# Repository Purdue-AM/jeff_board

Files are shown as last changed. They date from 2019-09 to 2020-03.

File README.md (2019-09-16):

# jeff_board
A straightforward Arduino Nano breakout board that allows for driving 2 PWM lines up to 30V, powered on 12/24V, and connects to two thermal sensors. 
-
The jeff board was designed to clean up two temperature sensors and a fan and heater driver into one breakout board, minimizing space occupied on the VAP print-head. Below is a list of the hardware on it, with a brief justification. This device is designed for academic research VAP machines, and is implemented on the systems at Herrick Labs at Purdue University.

<b>Components</b>

<b> Arduino Nano:</b> the Nano is a small-footprint implementation of the arduino uno with some changes to make it ideal for embedded project prototyping. More information can be found on the Arduino website (https://www.arduino.cc/en/Guide/ArduinoNano). The new Arduino Nano Every is a drop-in replacement, and is a bit cheaper. Note: there are hundreds of knock-off Arduino Nanos available for a quarter of the price, most of which will work with this board. If you're not comfortable debugging electronics issues, I recommend sticking to the original.

<b>MLX90614 IR Temperature Sensor:</b> Melexis makes great IR sensors that are easy to interface with over I2C. I used Adafruit's library for this (https://learn.adafruit.com/using-melexis-mlx90614-non-contact-sensors/wiring-and-test). This is where the ambient temperature is determined as well. In the future, moving to a tighter view-angle would be good (right now it's 90deg, sub-15deg would be great). 

<b>MAX31865 RTD Amplifier and Platinum RTD Sensor:</b> I chose an RTD sensor because the reservoir sensing needs to be really accurate right around room temp. We probably won't be heating the reservoir above around 40degC, so this is a good choice. I'm using a MAX31865 breakout board from Adafruit, but there's no reason that can't be added to the PCB in the future. In fact, I'd prefer it. 

<b>MIC4427 and various power MOSFETs:</b> the MIC4427 is a low-side MOSFET driver. This is necessary to avoid over-heating, since the Arduino Nano can't provide enough current to drive the gate capacitance quickly. This should also allow some robustness for knock-off arduinos. The specific power MOSFET isn't as important, as long as it's an N-Channel rated to at least 30Vds, has a low Rdon at Vgs of 5V or lower (this will often be called a logic-level power FET), and has the same pinout in a TO-220 package. For driving the fan, you're going to want a power MOSFET with a body diode. On the jeff board in HERL, I've used IRLB3034PbF which is an extremely robust power MOSFET.

<b>DC-DC Step-Down converter:</b> This board is designed to run off of the 3D printer power supply, both 12V and 24V models. You can use any linear or switching DCDC step-down converter that fits in the TO-220 footprint with the same pinout, but my preference is the Traco Power TSR series (https://www.tracopower.com/products/browse-by-category/show/dc-dc-converters/non-isolated-step-down-regulators/tsr-1/1/). These are really reliable and temperature tolerant, and the last thing we want is the temperature control board to lose power mid-print.

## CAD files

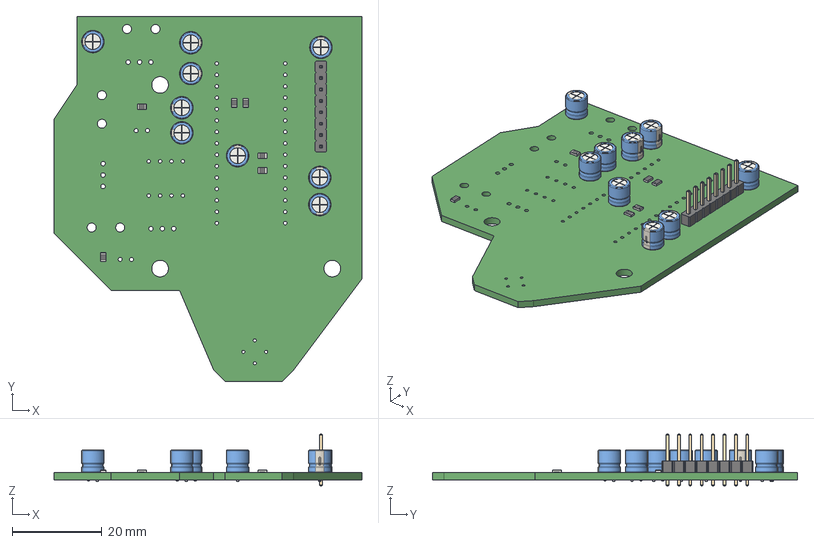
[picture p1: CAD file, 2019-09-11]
jeff_board_kicad/VAP_thermal_control.step
68.6 x 81.3 x 11.5 mm
LED_D5.0mm x 2
DIP-8_W7.62mm

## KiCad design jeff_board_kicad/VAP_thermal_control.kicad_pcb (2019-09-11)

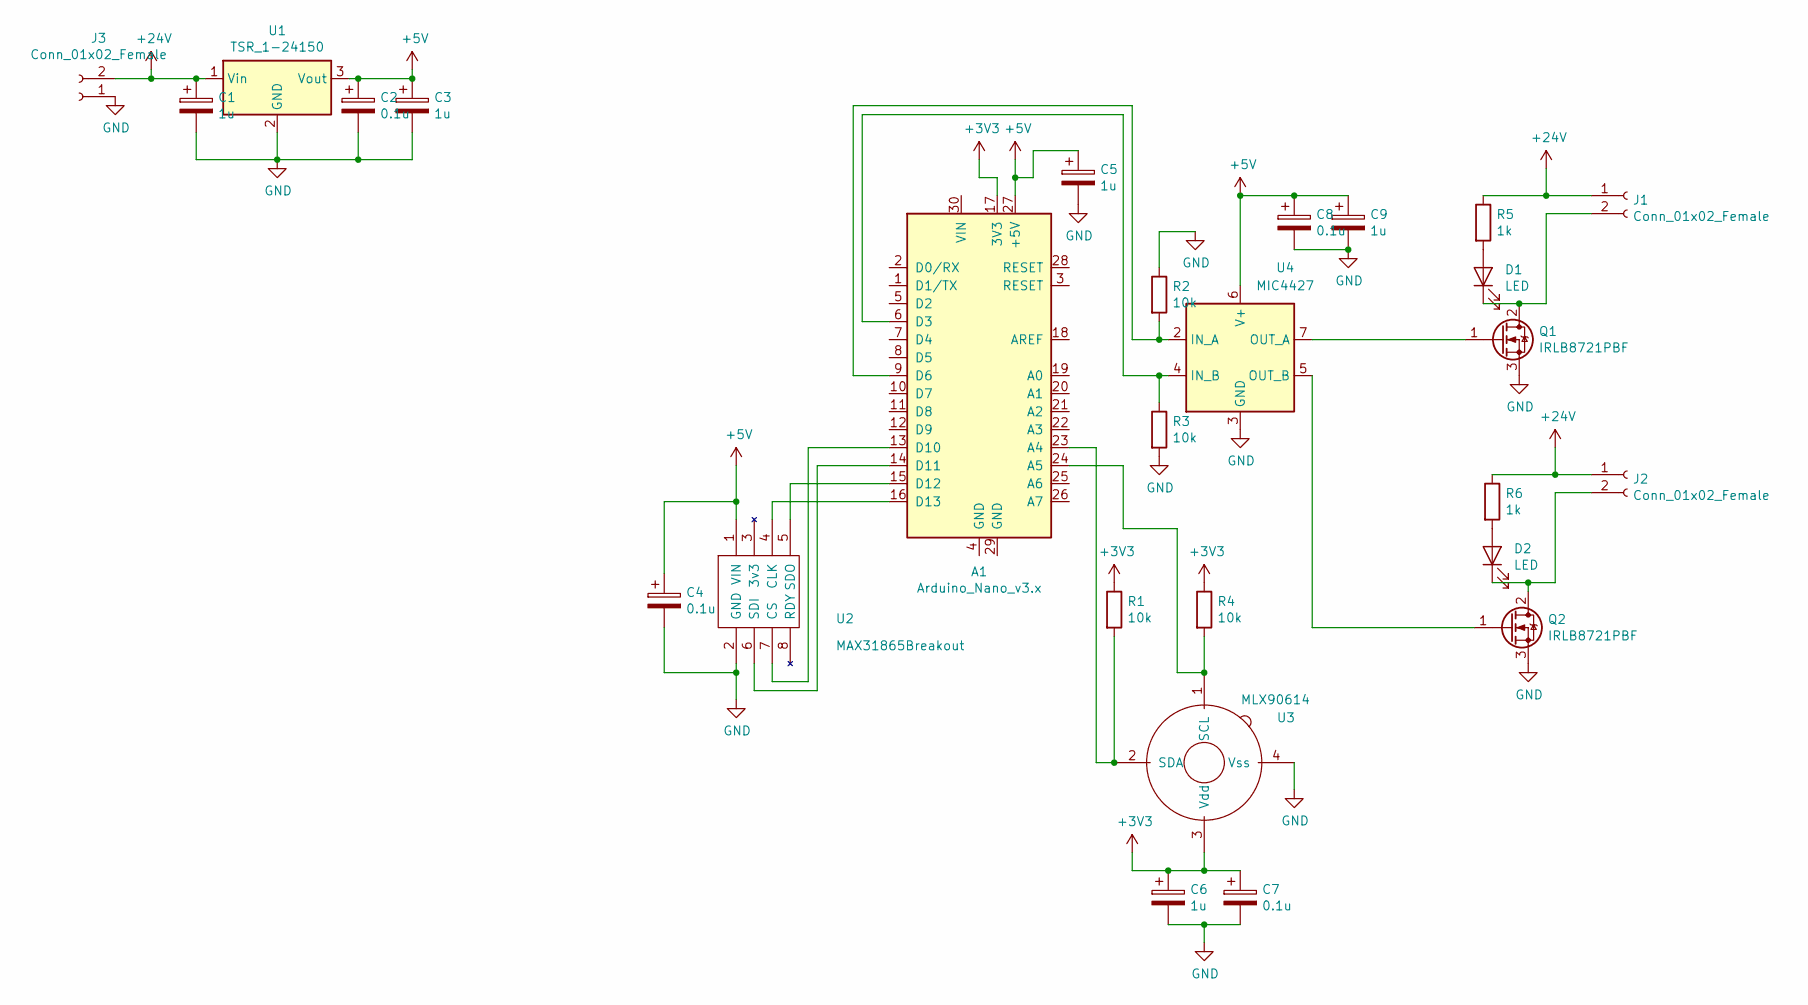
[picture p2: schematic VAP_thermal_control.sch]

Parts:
A1: Arduino_Nano_v3.x; Arduino_Nano
C1, C3, C5, C6, C9: 1u; CP_Radial_D5.0mm_P2.00mm
C2, C4, C7, C8: 0.1u; CP_Radial_D5.0mm_P2.00mm
D1, D2: LED; LED_D5.0mm
J1, J2, J3: Conn_01x02_Female; SolderWirePad_2x_2mmDrill
Q1, Q2: IRLB8721PBF; TO-220-3_Vertical
R1, R2, R3, R4: 10k; R_0805_HandSoldering
R5, R6: 1k; R_0805_HandSoldering
U1: TSR_1-24150; TO-220-3_Vertical
U2: MAX31865Breakout; Pin_Header_Straight_1x08_Pitch2.54mm
U3: MLX90614; TO-39-4_Window
U4: MIC4427; DIP-8_W7.62mm

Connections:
+3V3: A1.17 (3V3), C6.1, C7.1, R1.1, R4.1, U3.3 (Vdd)
+5V: A1.27 (+5V), C2.1, C3.1, C4.1, C5.1, C8.1, C9.1, U1.3 (Vout), U2.1 (VIN), U4.6 (V+)
+24V: C1.1, J1.1, J2.1, J3.2, R5.1, R6.1, U1.1 (Vin)
GND: A1.4 (GND), A1.29 (GND), C1.2, C2.2, C3.2, C4.2, C5.2, C6.2, C7.2, C8.2, C9.2, J3.1, Q1.3 (S), Q2.3 (S), R2.1, R3.2, U1.2 (GND), U2.2 (GND), U3.4 (Vss), U4.3 (GND)
unnamed: A1.6 (D3), R3.1, U4.4 (IN_B)
unnamed: A1.9 (D6), R2.2, U4.2 (IN_A)
unnamed: A1.13 (D10), U2.7 (CS)
unnamed: A1.14 (D11), U2.6 (SDI)
unnamed: A1.15 (D12), U2.5 (SDO)
unnamed: A1.16 (D13), U2.4 (CLK)
unnamed: A1.23 (A4), R1.2, U3.2 (SDA)
unnamed: A1.24 (A5), R4.2, U3.1 (SCL)
unnamed: D1.1 (K), J1.2, Q1.2 (D)
unnamed: D1.2 (A), R5.2
unnamed: D2.1 (K), J2.2, Q2.2 (D)
unnamed: D2.2 (A), R6.2
unnamed: Q1.1 (G), U4.7 (OUT_A)
unnamed: Q2.1 (G), U4.5 (OUT_B)

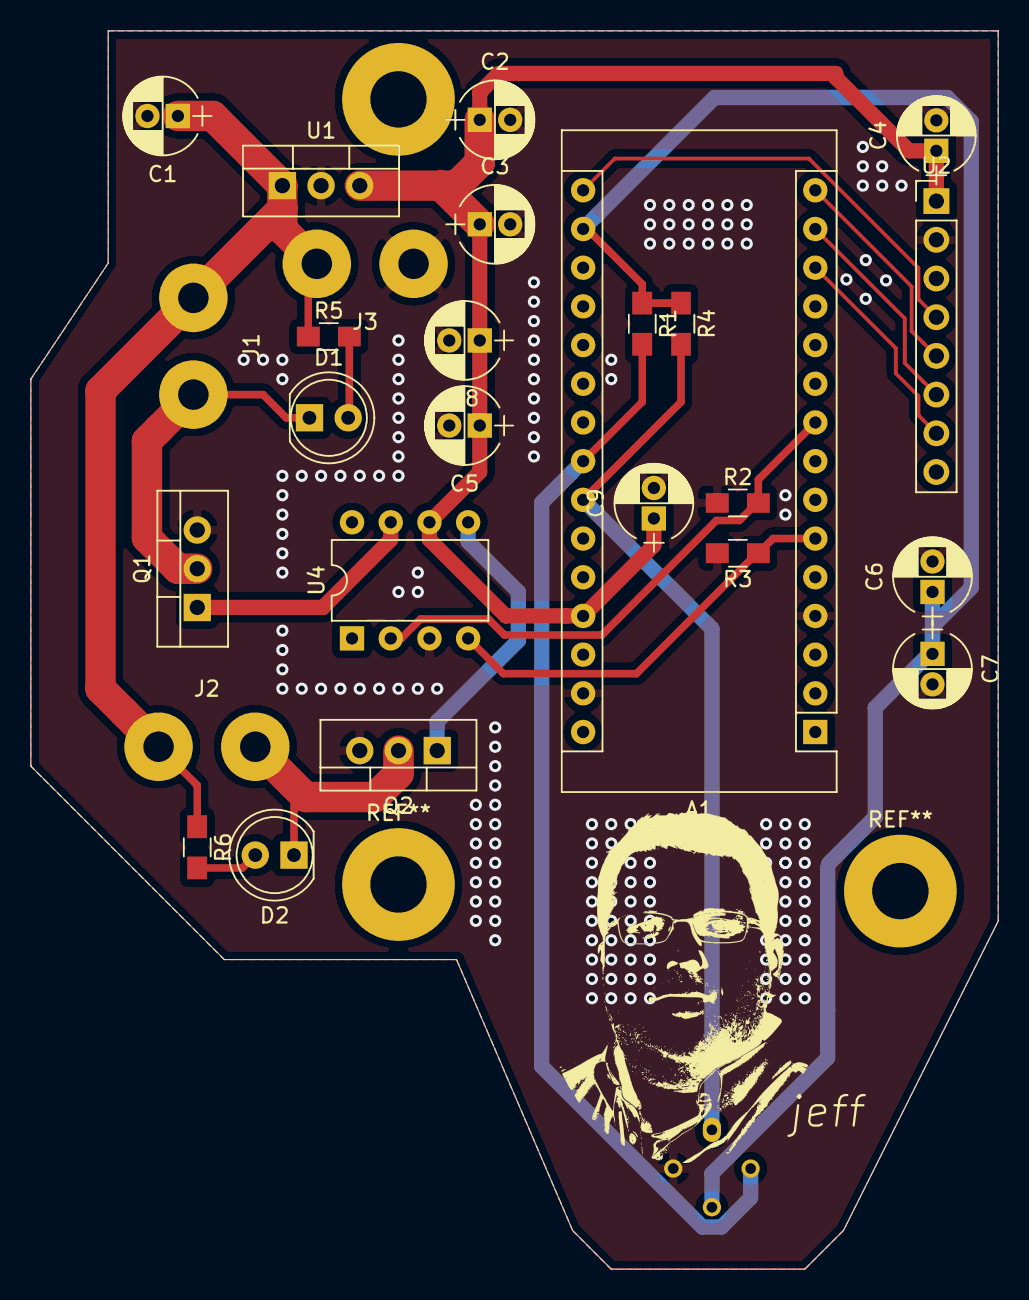
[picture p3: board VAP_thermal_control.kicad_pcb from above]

Board: 2 copper layers, 63.5 x 81.3 mm, 27 parts (1 on the bottom side), 18 nets.

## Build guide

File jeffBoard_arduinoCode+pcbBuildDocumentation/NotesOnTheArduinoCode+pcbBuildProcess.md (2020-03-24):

Author(s): Simon R.
Here are some notes about the arduino code and the build process of the Jeff board in March 2020.

*Arduino Code:*
The code provides a readout of RTD and IR sensor data over serial to a laptop running a serial monitor (such as the one included as part of the Arduino IDE).
To compile, it requires the Adafruit libraries for the MLX90614 IR sensor and the MAX31865 RTD breakout/reader which can be located within the links below.

https://learn.adafruit.com/adafruit-max31865-rtd-pt100-amplifier/arduino-code
https://learn.adafruit.com/using-melexis-mlx90614-non-contact-sensors/wiring-and-test

It would be nice if it wasn't necessary to use a laptop to read the sensor data. 
Adding a simple 16x2 display to solve this issue would be very easy.
Adafruit provides Arduino libraries that make interfacing with displays (such as the one linked below) very easy.
https://www.adafruit.com/product/181
And a Arduno library for this: https://learn.adafruit.com/character-lcds/arduino-code

*Notes on the PCB assembly process:*
The design specified SMD resistors of 0805 size, but 0603 were used instead as no 0805 were available. 
The actual resistance values were correct, and since the wattage being dissipated is quite low, the 0603 substitutes are functionally equivalent.

Ceramic caps of 0603 size were substituted in for the polarity-sensitive electrolytic caps that were implied in the pcb silkscreen and KiCad footprints.
The actual capacitance values were correct and are functionally equivalent.

*Finally:*
If making another board, please note that the mic4427ym component is not the correct package/footprint. It's important to note that as of March 2020, the footprint of the mic4427ym in the KiCad drawing does not reflect any available footprint of the mic4427ym as found on the web.
This may have been a design mistake, or simply the original package is no longer available. 
Either way: you can get around this by using a breakout board suitable for the mic4427ym IC itself and merging connections to the jeffBoard or by redesigning the footprint assignment on the jeffBoard to eliminate the mismatch.

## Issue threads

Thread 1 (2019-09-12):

24V PWM expansion

jcsmccaw, 2019-09-12:
The Arduino nano has the ability to drive 2 more designated PWM channels, more with software. Copying the MOSFET driving circuit in the current jeff would give more expansion spots to add powering lights, etc. Communication between the printer board (Mega) and the jeff (nano) could be set up through some header pins, i.e. one to enable/disable UV lights, one to enable/disable fan, etc.

jcsmccaw, 2019-09-21:
Started this in the branch jeff_boardV2. Layout is almost done, it just needs better mounting holes.

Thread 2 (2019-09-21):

Better mounting holes

jcsmccaw, 2019-09-21:
Current mounting holes are still inherited from old parts, and no longer make a lot of sense. Depending on the VAP head, changing these up is in order.

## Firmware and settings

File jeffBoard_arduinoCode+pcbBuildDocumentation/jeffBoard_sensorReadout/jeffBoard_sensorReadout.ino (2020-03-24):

//This sketch reads out the MLX90614 and MAX31865 board to serial at 115200 baud

#include <Adafruit_MAX31865.h>
#include <Wire.h>
#include <Adafruit_MLX90614.h>


Adafruit_MLX90614 mlx = Adafruit_MLX90614();


// Use software SPI: CS, DI, DO, CLK
Adafruit_MAX31865 thermo = Adafruit_MAX31865(10, 11, 12, 13);
// use hardware SPI, just pass in the CS pin
//Adafruit_MAX31865 thermo = Adafruit_MAX31865(10);

// The value of the Rref resistor. Use 430.0 for PT100 and 4300.0 for PT1000
#define RREF      430.0
// The 'nominal' 0-degrees-C resistance of the sensor
// 100.0 for PT100, 1000.0 for PT1000
#define RNOMINAL  100.0

void setup() {
  Serial.begin(115200);
  Serial.println("Adafruit MAX31865 PT100 Sensor Test!");

  thermo.begin(MAX31865_3WIRE);  // set to 2WIRE or 4WIRE as necessary


  Serial.println("Adafruit MLX90614 test");  

  mlx.begin();  
}


void loop() {

  //RTD portion of loop
  uint16_t rtd = thermo.readRTD();

  Serial.print("RTD value: "); Serial.println(rtd);
  float ratio = rtd;
  ratio /= 32768;
  Serial.print("Ratio = "); Serial.println(ratio,8);
  Serial.print("Resistance = "); Serial.println(RREF*ratio,8);
  Serial.print("Temperature = "); Serial.println(thermo.temperature(RNOMINAL, RREF));

  // Check and print any faults
  uint8_t fault = thermo.readFault();
  if (fault) {
    Serial.print("Fault 0x"); Serial.println(fault, HEX);
    if (fault & MAX31865_FAULT_HIGHTHRESH) {
      Serial.println("RTD High Threshold"); 
    }
    if (fault & MAX31865_FAULT_LOWTHRESH) {
      Serial.println("RTD Low Threshold"); 
    }
    if (fault & MAX31865_FAULT_REFINLOW) {
      Serial.println("REFIN- > 0.85 x Bias"); 
    }
    if (fault & MAX31865_FAULT_REFINHIGH) {
      Serial.println("REFIN- < 0.85 x Bias - FORCE- open"); 
    }
    if (fault & MAX31865_FAULT_RTDINLOW) {
      Serial.println("RTDIN- < 0.85 x Bias - FORCE- open"); 
    }
    if (fault & MAX31865_FAULT_OVUV) {
      Serial.println("Under/Over voltage"); 
    }
    thermo.clearFault();
  }
  Serial.println();

  //IR Sensor portion of loop
  Serial.print("Ambient = "); Serial.print(mlx.readAmbientTempC()); 
  Serial.print("*C\tObject = "); Serial.print(mlx.readObjectTempC()); Serial.println("*C");
  Serial.print("Ambient = "); Serial.print(mlx.readAmbientTempF()); 
  Serial.print("*F\tObject = "); Serial.print(mlx.readObjectTempF()); Serial.println("*F");

  Serial.println();

  
  delay(1000);
}

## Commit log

2019-09-11 V0.1 Board Layout
    Based on the original VAP thermal controller, this is the V0.1 layout (corrected grounding fill error on the arduino pinout)
    [VAP_thermal_control-B_Cu.gbr, VAP_thermal_control-B_Mask.gbr, VAP_thermal_control-B_Paste.gbr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]
2019-09-16 Update README.md
    description of what components are on the board, what they do.
